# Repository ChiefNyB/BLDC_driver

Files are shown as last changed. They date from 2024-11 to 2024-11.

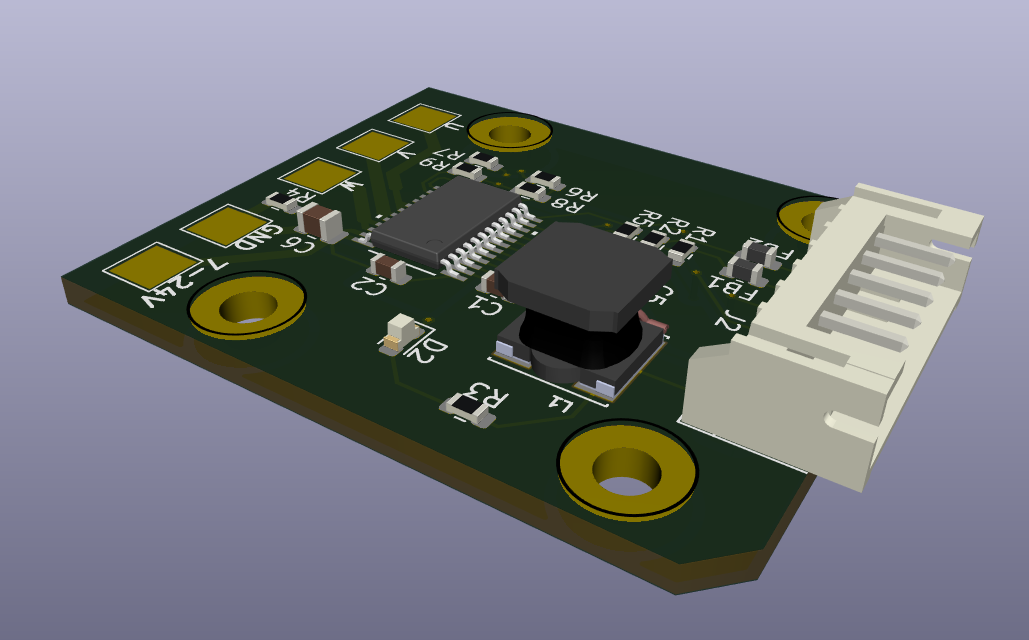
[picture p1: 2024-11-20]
assets/assembly2.png

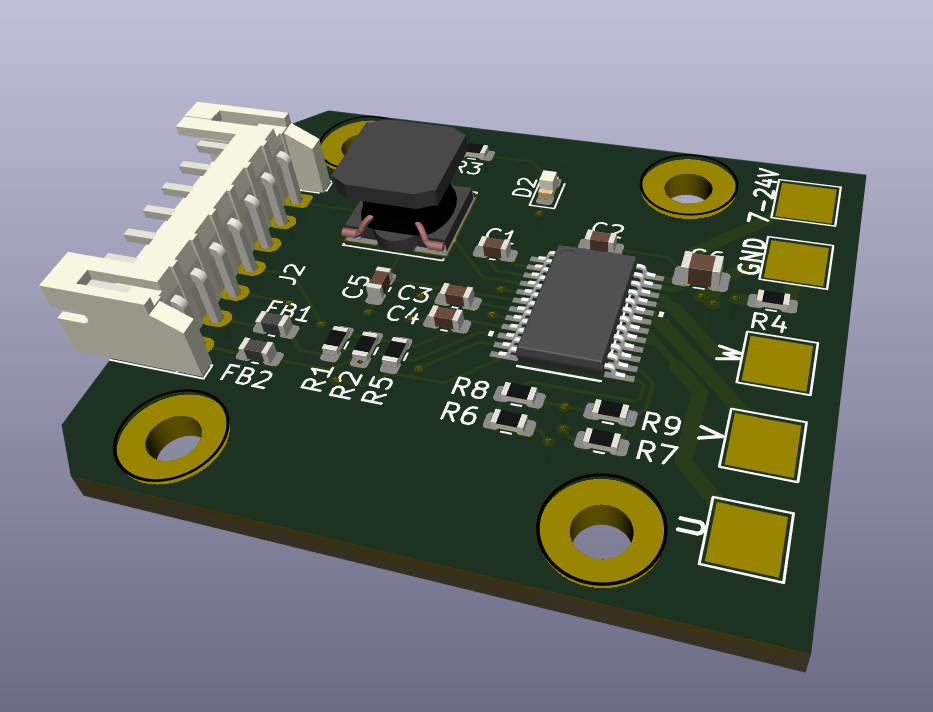
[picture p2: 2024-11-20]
assets/assembly.png

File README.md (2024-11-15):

# BLDC driver
 [TI DRV10983-Q1](https://www.ti.com/product/DRV10983-Q1/) based BLDC motor controller

 Development software: KiCad 8.0.5 (latest)

 ## *Üzenet*

 Szerintem majd ide a README-be írogathatjuk dokumnetáció vázlatos részét,
 a számítást meg Excelbe vagy valami python scriptbe lehet nyomni
 (ugyanígy version controllozva), aztán innen aztán mehet majd Word-be a bővebb leírás.

 Éés szerintem nyugodtan írogathatunk ide kommenteket is, talán kevésbé veszik
 el mint a chatben.

 Légyszi nézzétek meg a katalógust is (bent van a datasheet mappában), meg az áramkört is,
 igyekeztem leírni a dolgokat amiket csináltam. Mindezek alapján remélem, hogy nektek is érthető lesz majd, hogy mi mit csinál.
 Ha bármi kérdésetek van, írjátok akár ide valahova, akár messengeren. Légyszi mindketten olvassátok el az egész README-t!
 Köszi :)

 Ide kigyűjtöttem, hogy szerintem még mi kell:

 ## További lépések (nagy vonalakban)

  - Komponensek értékeinek kiszámítása --> komponensek választása
  - Fizikai layout kialakítása
  - (adhatnánk majd a hozzá passzoló motorokra egy példát)

## Dokumentáció vázlatosan (kapcsolás)
(ömlesztett gondolatok, egy csöppet össze-vissza)

KORREKCIÓ: A TVS DIÓDÁT EGYENLŐRE KISZEDTEM, VAN BEÉPÍTETT A CHIPBE
  
  - a chip modellt (footprint, stb...) a
  TI-os lapról töltöttem és illesztettem be: [link](https://vendor.ultralibrarian.com/TI/embedded/?gpn=DRV10983-Q1&package=PWP&pin=24&sid=&c=0)
  (lementettem saját global libraryba... ha nektek valami miatt nem látszódna, akkor
  ezt lehet nektek is meg kell csinálni)
  - IC bekötése a datasheet 64. oldalán található 71.figureban, egy csomó komponens (főleg kondik) értéke innen van
  található kapcsolás alapján (lehet arról írni esetleg, hogy milyen funkciói vannak
  az IC-nek)
    - 12Vról megy, (esetleg 24V, de ha 28-ig visszatölt, akkor már egyébként lekapcsolja a powerstaget)
    - I2C max 400kHz
    - milyen lekapcsolási-biztonsági funkciók vannak (Over voltage, o.current, thermal shutdown...)
  - a schematic hierarhikus, több lapból áll (drive, power), de nem is biztos hogy szükség lenne rá, mert elég egyszerű,
  csak kicsit fancybb és esetleg segíti a logikát átlátni
  - a pontos típus: [DRV10983SQ](https://www.ti.com/product/DRV10983-Q1/part-details/DRV10983SQPWPRQ1) legyen, ha standby modeban is 
  használni szeretnénk az 5V-os buck convertert --> mikrovezérlő meghajtható róla (ld. katalógus 3.o.)
  - I2C védelmet és szűrést [ez](https://www.we-online.com/components/media/o734709v410%20ANP121a%20%20Filter%20and%20surge%20protection%20for%20I2C%20Bus%20EN.pdf)
  alapján csináltam --> itt javasolt komponensekkel (ferrit gyöngy és TVS dióda) megegyező paraméterűeket lesz majd érdemes választani
  (egyenlőre egy kb hasonlót raktam be)
  - terveim szerint csinálok 2 verziót:
    - csatlakozós (Táp & motor is csatlakozós)
    - beforrasztós (táp& motornak csak pad-ek vannak amikre majd rá lehet forrasztani a vezetékeket)
    (ez az ahol a testpoint (TP) nevű kivezetések vannak)
  - a TI IC alatt a túloldalon van egy PAD (majd thermal viákkal összekötve) a GND-hez kötve, hogy hőt disszipáljon
  és ide lehet(ne) rakni majd a hűtőbordát is
  - van egy sima GND és egy PWRGND, hogy a motor áramai minél kevésbé zavarjanak bele a digitális jelekbe, ezek össze vannak kötve egy 0ohmos ellenállással
  - az 5V (output) jelenlétét LED jelzi
  - decoupling capacitorok közel az IC-hez (majd a kialakításnál fizikailag)
  - minden jel-bemenet és kimenet, ami ki van vezetve (SCL, SDA, FG, SPEED, DIR) 3V3 TVS diódával védve ESD ellen
  - I2C csak 3V3 szinten mehet
  - FG pin 3V3-as impulzusokat ad (to be checked in datasheet)
  - DIR és SPEED bemeneten használható 5V-os jel (azaz megtáplálható egy sima potiról és kapcsolóról, ennek az egy panelnek a segítségével)
    - viszont ehhez előbb I2C-n be kell konfigurálni
    - a bemenetek egy-egy feszültségosztóval le vannak skálázva 3v3-ra
    - ehhez majd lesznek számítások, poti értéke
  - a legvégén esetleg kérhetünk majd árajánlatot ha unatkozunk :P

  - az I2C-t úgy lehet használni, ha a külső áramkör GND-je össze van kötve a motordriver GND_D-jével
  - az 5V-os bemenet használatához is legalább a GND-t kell bekötni

  ## Szükséges számítások, paraméterek
  Légyszi Kristóf ide, vagy valami fileba majd gyűjtsd ki a komponens nevét/számát (pl.: R1) és a linket hogy melyiket választottuk...
  Majd belepakkolom a schematicba és generálok belőle egy BOM .csv filet.
  ( Lehetséges oldalak: farnell, rs-online, lomex, TME ...ilyesmik. Csak legyen magyar oldal! )
  (Esetleg lehet egy specifikus motor amit kinézünk, és annak a pramaétereit is felhasználjuk a számításokhoz)

  - elsősorban a TI-os katalógus alapján, a typical application résznél van egy lista hogy ők mit javasolnak
  - csak SMD alkatrészeket please
  - alapból ilyen 0603-as (mármint inches 0603, mert a metrikus méretek el vannak tolva) méretű ellenállásokat és kondikat stb. keresünk,
  esetleg kicsit kisebb vagy nagyobb (de nyilván ha nagyobb kell, akkor nagyobb kell, pl valszeg a táp kondija az gyanús, hogy nagyobb)
    - ellenállás választásnál ki kell számolni a teljesítményét és aszerint kell választani (0.25W; 1W ...)
    - LED-nél választani kell egy LED-et, majd az ahhoz előírt mA-hez választunk egy ellenállást, a színét rád bízom Kristóf ;)
    - kondiknál a feszültséget és a kapacitást kell nézni alapból
    - SPEED és DIR inputokra olyan feszültségosztó kell (ellenállásértékek), amik leskálázzák a bejövő 5V-ot 3,3-ra
  - I2C védelem: ld. dokumentáció vázlatpontjai közt, illetve ezek alapján még újra számíthatók a felhúzó ellenállások értékei is
  - ha nagyon fancy-k akarunk lenni, egy thermal calculationt is nyomhatunk és esetleg egy hűtőbordát is válasszunk (1. gyakorlat -> pdf kb. 10. oldal)
  - TVS diódák kapcsolása nem látszik a kapcs rajzon de az assets mappában megtalálható

  ## Kiválasztott alkatrészek
  Feltöltöttem egy Excel táblában a katalógusokból kiválasztott áramköri elemeket. A dokumentációhoz ideírom, amit csináltam:

  - Katalógusból kiválasztottam az ajánlások miatt előre ismert áramköri elemeket + a LED-et
  - Három kis számolás volt:
    - LED ellenállás,
    - feszültségosztók (TI online számolójával: [link](https://www.ti.com/download/kbase/volt/volt_div3.htm)),
    - I2C felhúzó ellenállások min-max értékeinek újraszámolása (az ajánlottak jók maradtak).

  Minden számolás és az összes alkatrész az Excelben. Alkatrészekhez van típuszsám, link, footprint adat és méretezési feltétel is (ha volt).
  A termikus számítások nem voltak kivitelezhetők, nincs elég adat veszteségekre vagy case-sink hőellenállásra (vagy hogy egyáltalán becsüljük).
  Elvileg a driver alá kerülő thermal pad elegendő, bele lehet írni a dokumentációba, hogy igény szerint lehet még adni hozzá.

  ## PCB alias NYÁK design
  - csatolásmentesítő kondik közel az IC-hez, mindegyiknek saját viája van a GND-hez
  - 45°-os track törésszögek a jelreflexió elkerülésére
  - thermal via-k: 20mil hole diameter, 8mil hole (for least resistance) ahogy [itt](https://www.ti.com/lit/an/slva959b/slva959b.pdf) a 2.5-ben írják
  - a teljesítményfolyamban lévő track-ek és viák méretezve vannak (viából van egy dupla is, bár nem feltétlen lenne rá szükség) 
  a számításokról készített screenshot az assetsben
  - digitális <--> teljesítény oldalak elválasztása fizikailag amennyire lehet
  - teljesítményvonalak kialakításánál fontos volt, hogy minél kisebb loopot csináljanak és rövidek legyenek
  - GND és GNDPWR egy 0ohmos ellenállással (R4) összekötve: kis vezetékellenállású összeköttetés a bemeneti GND és a digitális jelek
  GND-je közt
  - buck konverter trackjei default értéken vannak, de van róla számítás hogy elég (assetsben)
  - a power bemenetek jelölve vannak, a csatlakozónál légyszi csinálj egy ábrát, ami "katalógusba" mehetne
  - két sarokban letörések...mert csak... :P 
  - M2.5-ös mounting holeok hogy lehessen odacsavarozni valahova
  - az alsó oldalra ragasztható heatsink ha akarja a felhasználó, de figyelni kell,
  hogy ezen a részen galvanikus kapcsolat ne alakuljon ki a külvilággal
  - földkiöntés a sima GND-vel
  (- esetleg át lehetne alakítani hogy a heatsink-pad a sima GND-hez kapcsolódjon és a PWRGND-t másmerre vezetni, ha van idő...)
  - ... és ezeken kívül bármi amit látsz a boardon és érdemes leírni

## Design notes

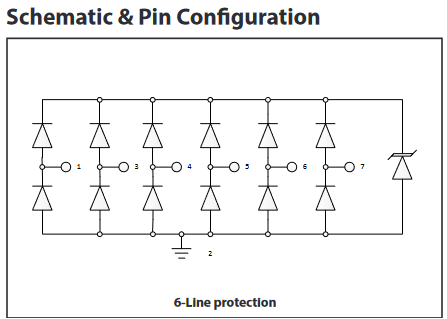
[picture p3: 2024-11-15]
assets/TVS_schematic.png

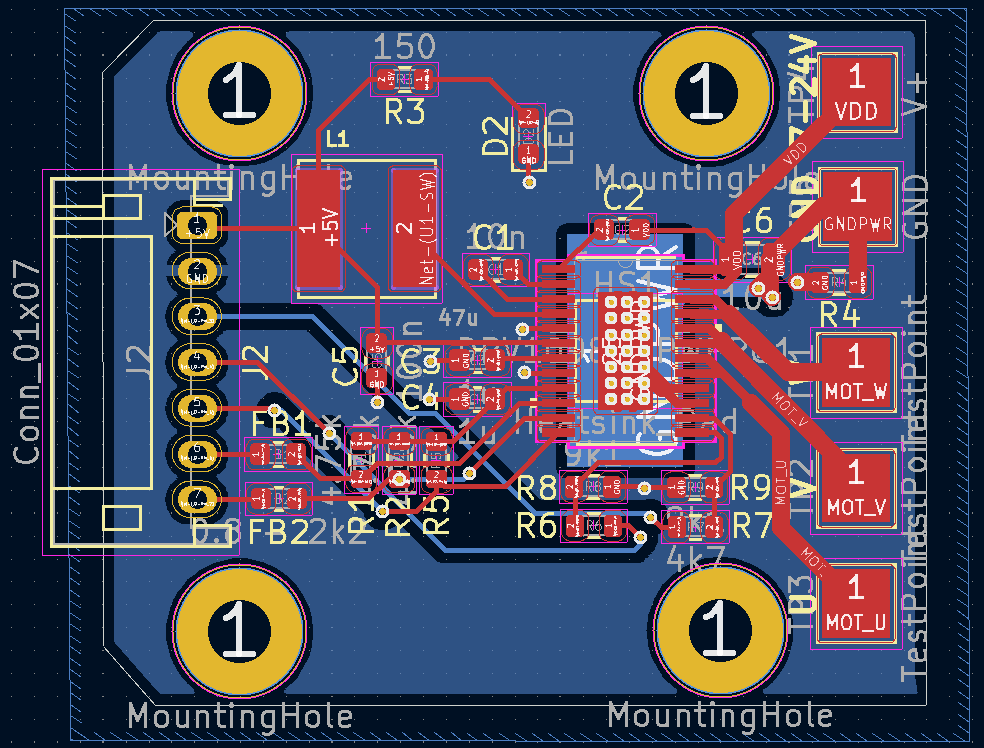
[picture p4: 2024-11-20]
assets/PCB_design.png

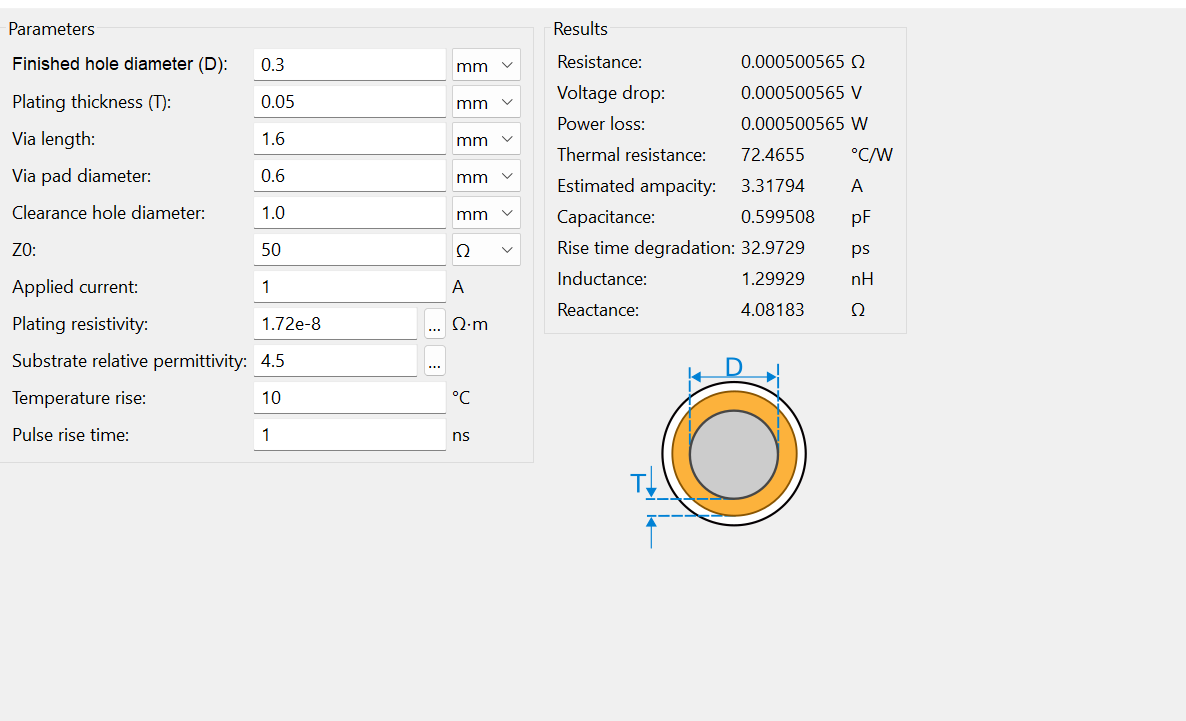
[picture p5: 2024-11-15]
assets/via current calculation.png

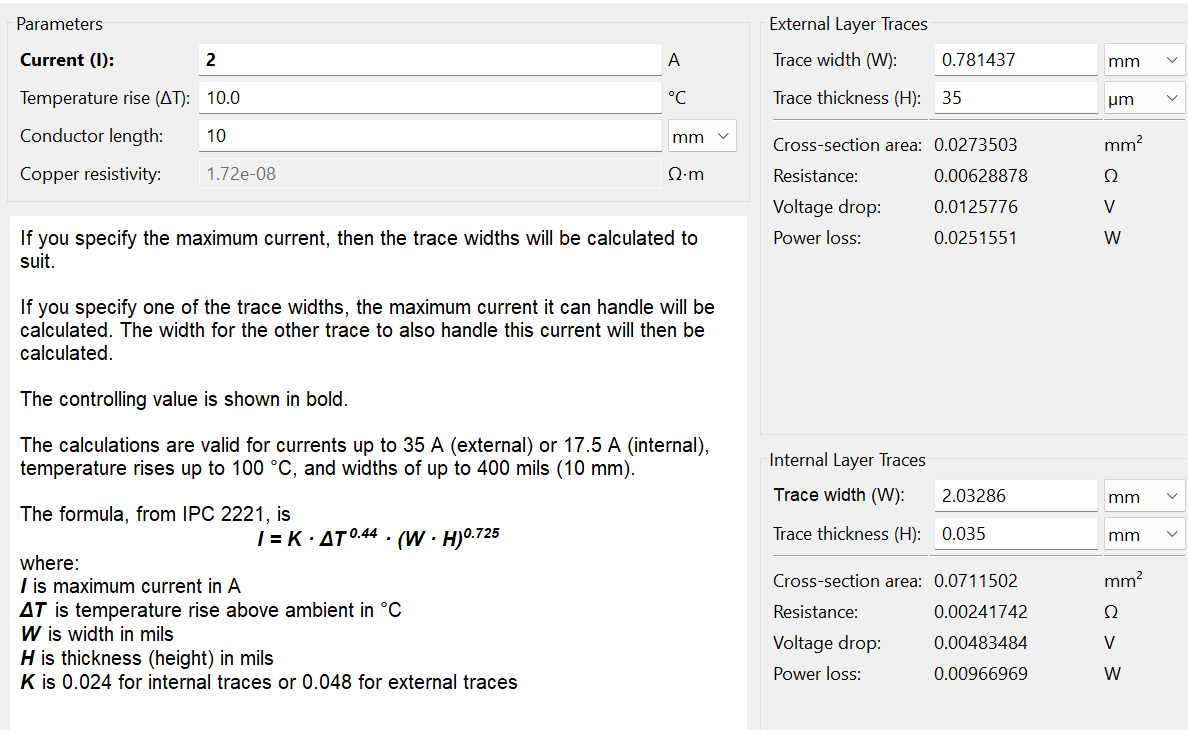
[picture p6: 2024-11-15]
assets/track width calculation.png

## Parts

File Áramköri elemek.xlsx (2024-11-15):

Jelölés | Érték | Típus | Link | Footprint |  | Méretezve
C1 | 10n | CC0603KPX7R0BB103 | https://hu.farnell.com/yageo/cc0603kpx7r0bb103/capacitor-0-01uf-x7r-0603/dp/4255277 | Van letölthető | 0603 | Max VCC = 48 V, biztosági tényezővel < 100 V
C2 és C5 | 100n | GRM188R72A104KA35D | https://hu.farnell.com/murata/grm188r72a104ka35d/cap-0-1-f-100v-10-x7r-0603/dp/1828921 | Van letölthető | 0603 | Max VCC+6 V < 100V
C3 és C4 | 1u | CC0603KRX7R7BB105 | https://hu.farnell.com/yageo/cc0603krx7r7bb105/cap-1-f-16v-10-x7r-0603/dp/1458900 | Van letölthető | 0603 | Max V3P3, biztonsági tényezővel < 16 V
C6 | 10u | GRM188R61E106KA73D | https://www.digikey.hu/hu/products/detail/murata-electronics/GRM188R61E106KA73D/9867922 | Van letölthető | 0603
L1 | 47u | VLS6045EX-470M | https://www.digikey.hu/hu/products/detail/tdk-corporation/VLS6045EX-470M/5286703 | Van letölthető | 0645 | Min. 1.15A, max. 1 Ohm |  | U_max
R1, R2 és R5 | 4.75k | RC0603FR-074K75L | https://hu.farnell.com/yageo/rc0603fr-074k75l/res-4k75-1-0-1w-0603-thick-film/dp/3495864 | Van letölthető | 0603 | 0.003368421053 | W | 4 | V
R3 (LED) | 150 | RC0603FR-07150RL | https://hu.farnell.com/yageo/rc0603fr-07150rl/res-150r-1-0-1w-0603-thick-film/dp/9238387 | Van letölthető | 0603 | 0.06 | W | 0.02 | A
R4 | 0 | RC0603FR-130RL | https://hu.farnell.com/yageo/rc0603fr-130rl/res-1a-0-1w-thick-film-0603/dp/4312015RL | Van letölthető | 0603
R6 és R7 | 4.7k | AT0603BRB074K7L | https://hu.farnell.com/yageo/at0603brb074k7l/res-4k7-0-1-0-1w-thin-film-0603/dp/4047053 |  | 0603 | 0.005319148936 | W | 5 | V
R8 és R9 | 9.1k | AT0603BRD079K1L | https://hu.farnell.com/yageo/at0603brd079k1l/res-9k1-0-1-0-1w-thin-film-0603/dp/4047064 |  | 0603 | 0.001196703297 | W | 3.3 | V
D1 | TVS diode array | PESD4USB3UTTS-QX | https://hu.mouser.com/ProductDetail/Nexperia/PESD4USB3UTTS-QX?qs=3Rah4i%252BhyCFcdVR8DwXcmg%3D%3D | Van letölthető | DFN-2510D-10 | 3.3 V operating voltage
D2 | LED | 150060VS55040 | https://www.digikey.hu/hu/products/detail/w%C3%BCrth-elektronik/150060VS55040/8557182 | Van letölthető | 0603
FB1 és FB2 | – | 782631222 | https://hu.farnell.com/wurth-elektronik/782631222/ferrite-bead-2-2-kohm-0-15a-0603/dp/3551396 | Van letölthető | 0603
Számolás
R3
Continuous Forward Current | 0.02 | A
Niytóirányú feszültség | 2.0 | V
Forrásfeszültség | 5.0 | V
LED ellenállás: | 150 | Ohm
Feszültségosztók
U_be | 5 | V
U_ki | 3.3 | V
Kalkulátor: | https://www.ti.com/download/kbase/volt/volt_div3.htm
 | (Standard méretű ellenállások kereséséhez feszültségosztóhoz)
R1 | 4.7k | Ohm
R2 | 9.1k | Ohm
I2C felhúzó ellenállások (f = 400 kHz)
Referencia-feszültség | 3.3 | V (dokumentációból)
Maximum logikai 0 feszültség | 0.6 | V (dokumentációból)
Max parazita busz-kapacitás | 6.5e-13 | F (400 kH)
Maximum engedélyezett felszállási idő | 3e-07 | s (400 kHz)
Maximum lehetséges áram | 0.003 | A (400 kHz)
R_min | 900 | Ohm
R_max | 544716.7019 | Ohm
Maradhat a 4.75 kOhm

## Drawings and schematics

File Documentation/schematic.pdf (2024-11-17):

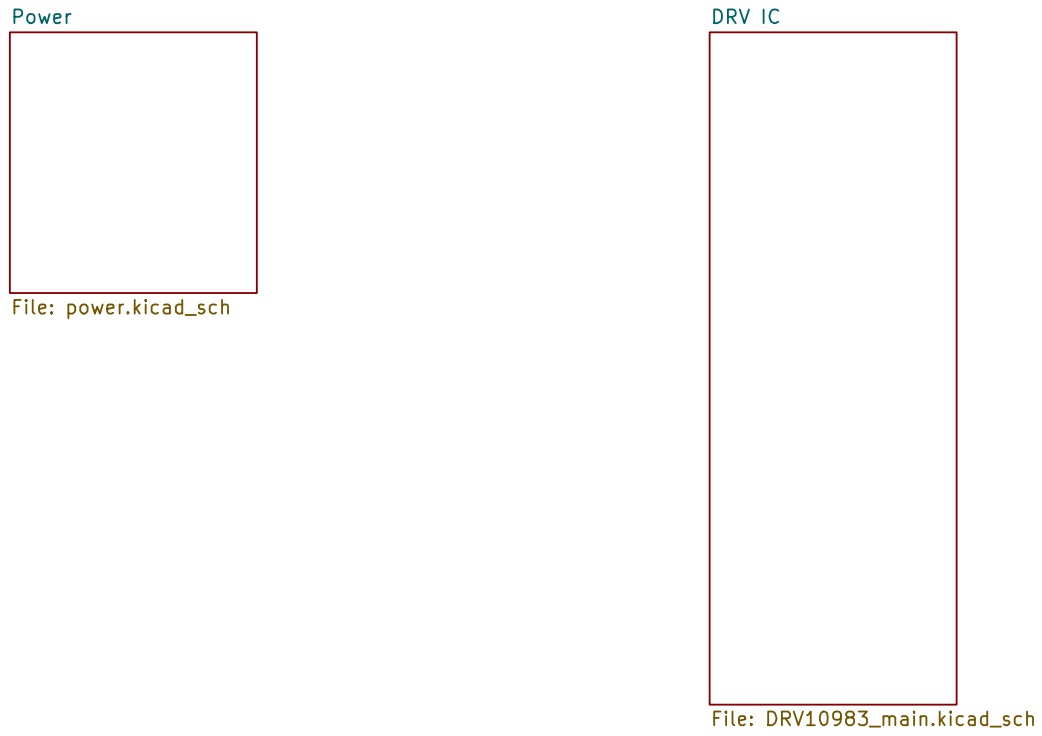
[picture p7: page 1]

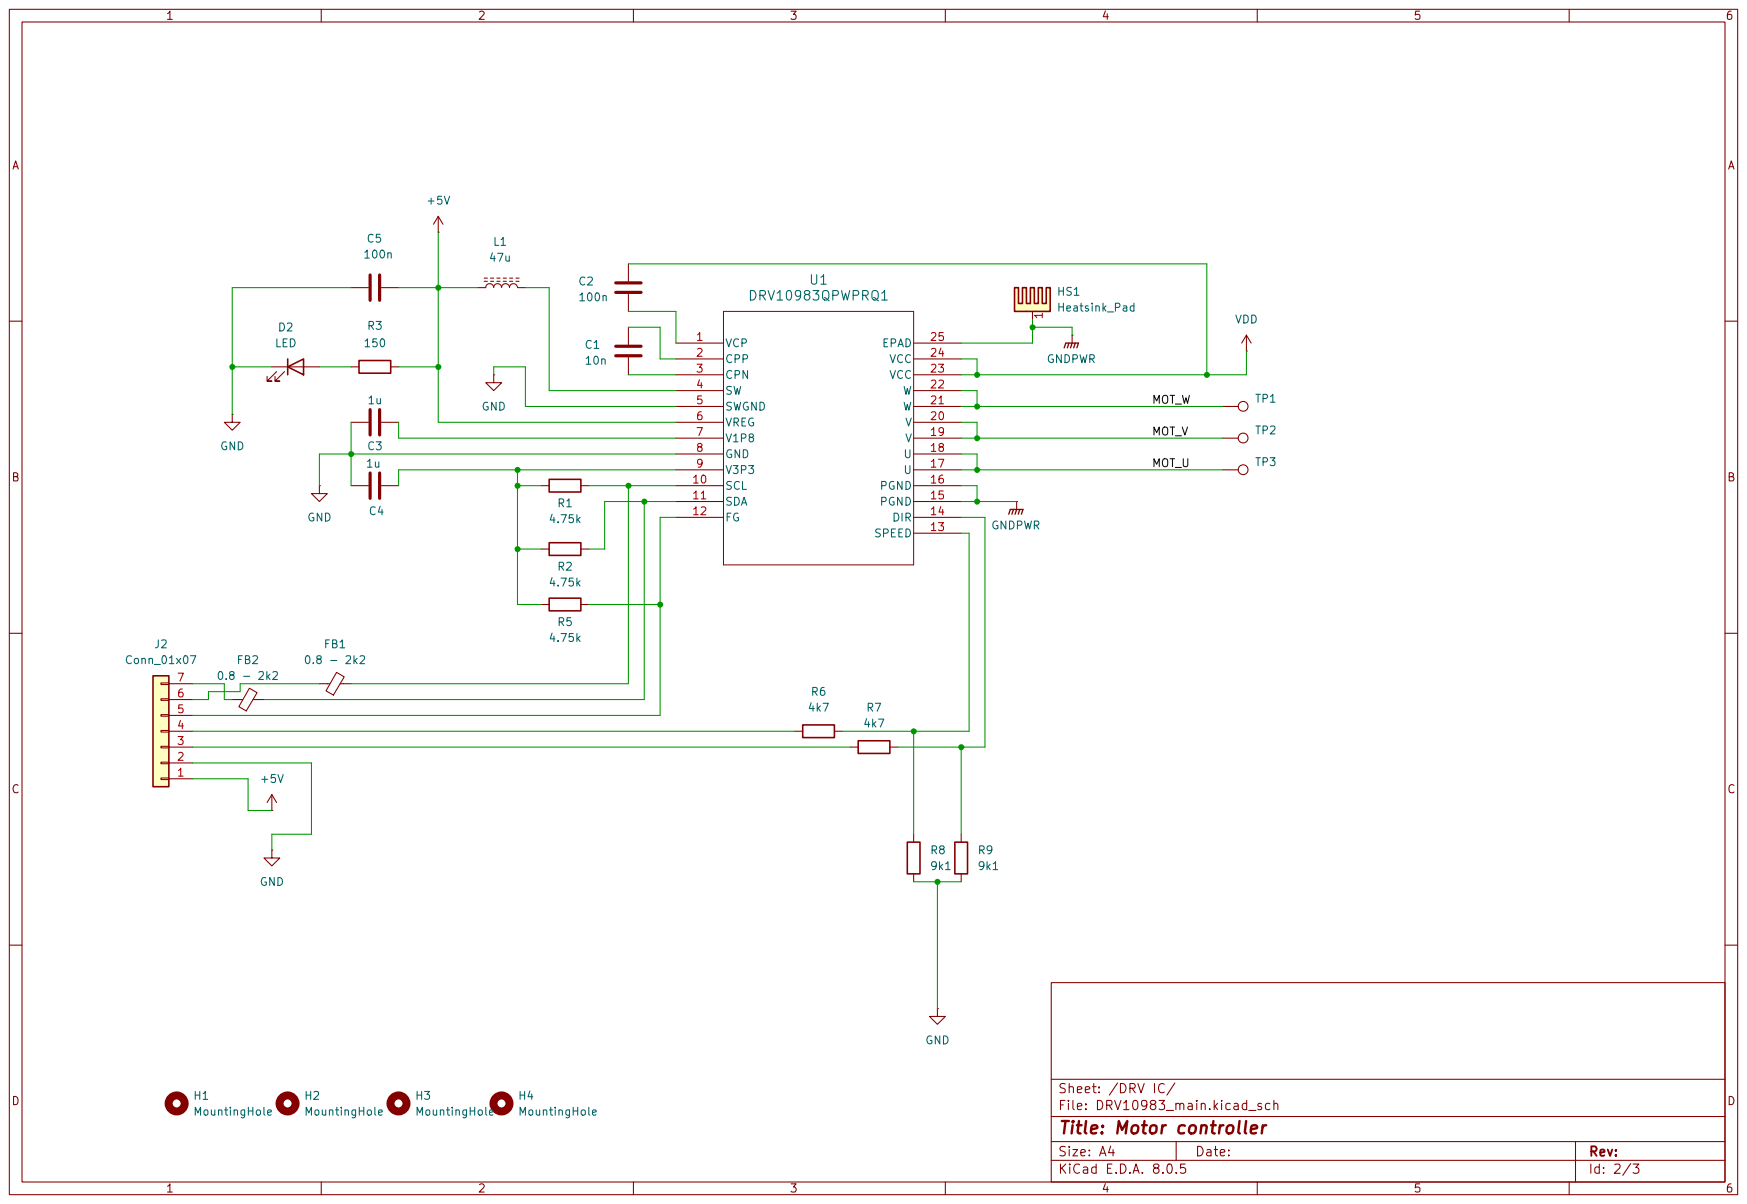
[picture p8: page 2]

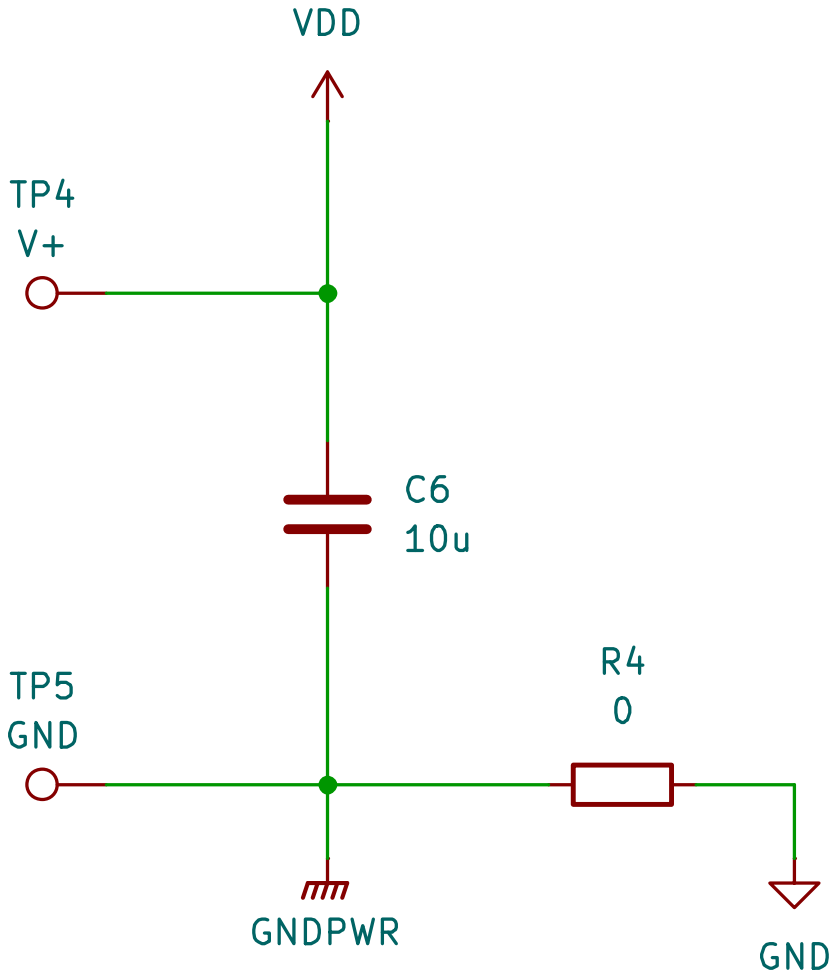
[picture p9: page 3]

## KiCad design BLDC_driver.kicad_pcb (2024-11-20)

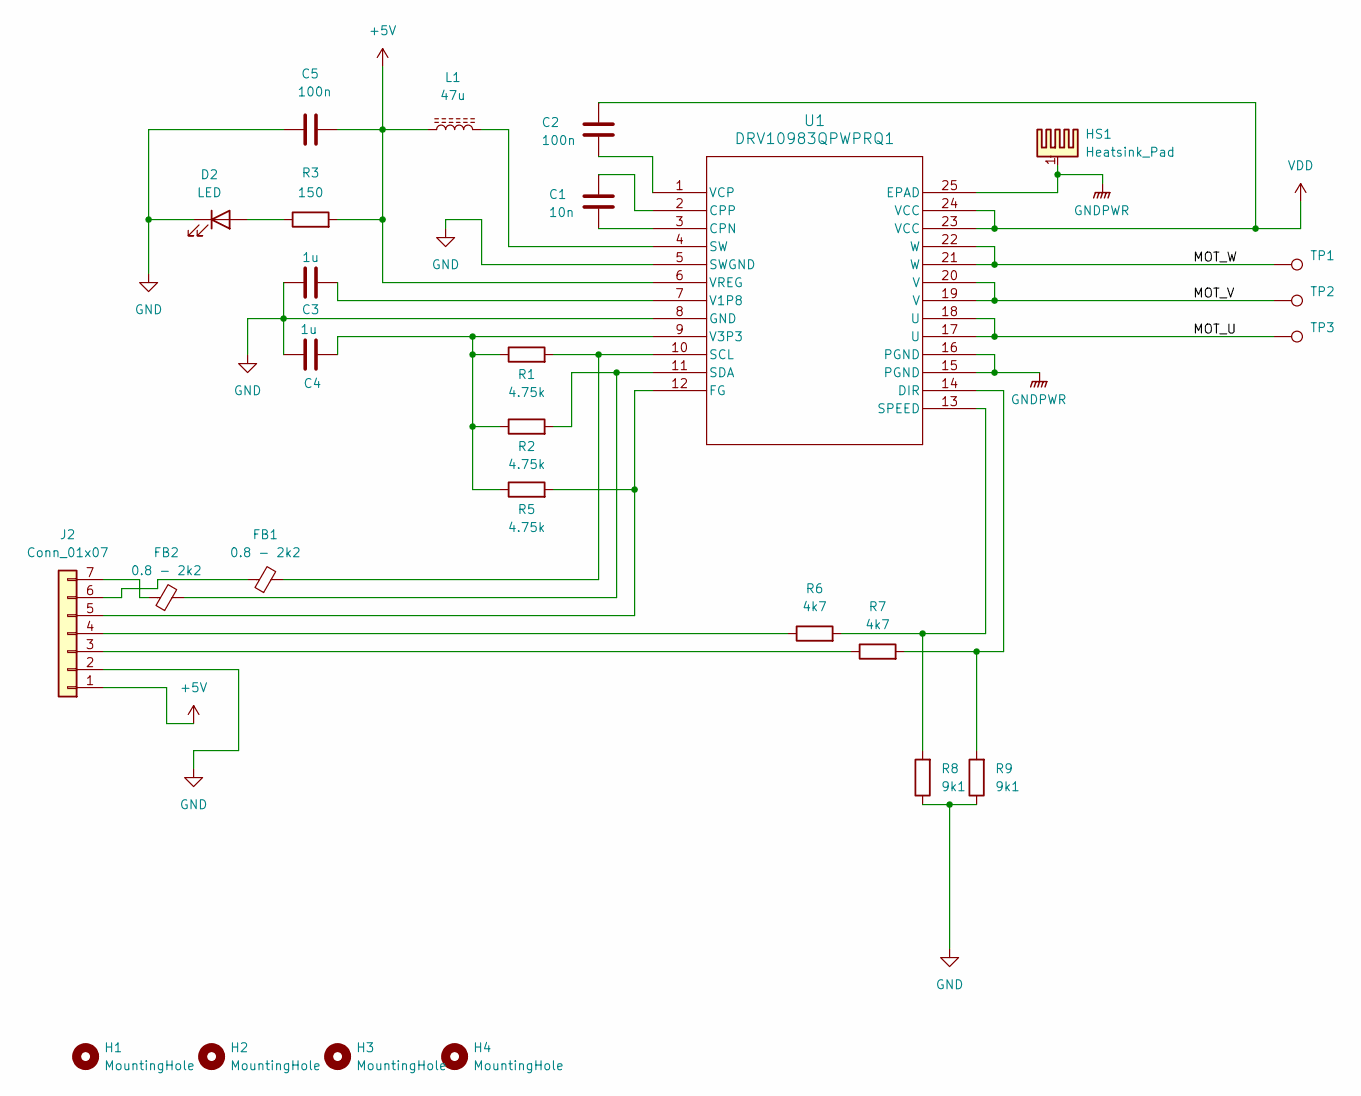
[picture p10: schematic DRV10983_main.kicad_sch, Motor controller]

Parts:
C1: 10n; C_0603_1608Metric
C2, C5: 100n; C_0603_1608Metric
C3, C4: 1u; C_0603_1608Metric
D2: LED; LED_0603_1608Metric
FB1, FB2: 0.8 - 2k2; L_0603_1608Metric
H1, H2, H3, H4: MountingHole; MountingHole_2.7mm_Pad
HS1: Heatsink_Pad; TestPoint_Pad_4.0x4.0mm
J2: Conn_01x07; JST_PH_S7B-PH-K_1x07_P2.00mm_Horizontal
L1: 47u; IND_VLS6045EX-470M
R1, R2, R5: 4.75k; R_0603_1608Metric
R3: 150; R_0603_1608Metric
R6, R7: 4k7; R_0603_1608Metric
R8, R9: 9k1; R_0603_1608Metric
TP1, TP2, TP3: TestPoint; TestPoint_Pad_3.0x3.0mm
U1: DRV10983QPWPRQ1; PWP24_2P4X5P16_TEX

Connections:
+5V: C5.2, J2.1, L1.1, R3.2, U1.6 (VREG)
/DRV IC/MOT_U: TP3.1, U1.17 (U), U1.18 (U)
/DRV IC/MOT_V: TP2.1, U1.19 (V), U1.20 (V)
/DRV IC/MOT_W: TP1.1, U1.21 (W), U1.22 (W)
GND: C3.1, C4.1, C5.1, D2.1 (K), J2.2, R8.1, R9.1, U1.5 (SWGND), U1.8 (GND); also elsewhere on the board
GNDPWR: HS1.1, U1.15 (PGND), U1.16 (PGND), U1.25 (EPAD); also elsewhere on the board
unnamed: D2.2 (A), R3.1
unnamed: J2.3, R7.1
unnamed: J2.4, R6.1
unnamed: J2.5, R5.2, U1.12 (FG)
unnamed: FB1.1, J2.6
unnamed: FB2.1, J2.7
unnamed: C1.2, U1.3 (CPN)
unnamed: C1.1, U1.2 (CPP)
unnamed: R7.2, R9.2, U1.14 (DIR)
unnamed: FB1.2, R1.2, U1.10 (SCL)
unnamed: FB2.2, R2.2, U1.11 (SDA)
unnamed: R6.2, R8.2, U1.13 (SPEED)
unnamed: L1.2, U1.4 (SW)
unnamed: C3.2, U1.7 (V1P8)
unnamed: C4.2, R1.1, R2.1, R5.1, U1.9 (V3P3)
unnamed: C2.2, U1.1 (VCP)
VDD: C2.1, U1.23 (VCC), U1.24 (VCC); also elsewhere on the board

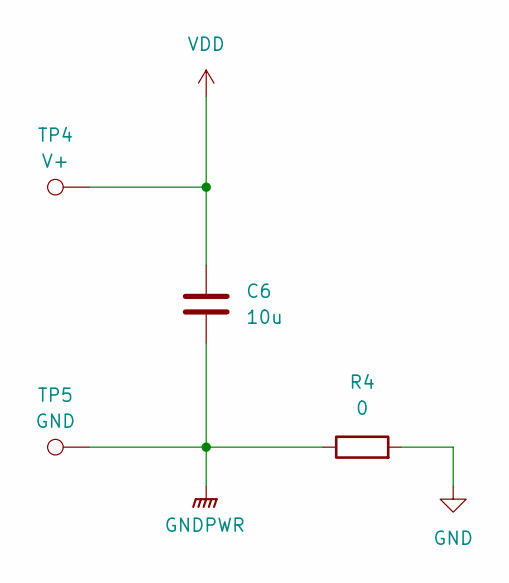
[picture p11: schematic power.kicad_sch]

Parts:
C6: 10u; C_0805_2012Metric
R4: 0; R_0603_1608Metric
TP4: V+; TestPoint_Pad_3.0x3.0mm
TP5: GND; TestPoint_Pad_3.0x3.0mm

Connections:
GND: R4.2; also elsewhere on the board
GNDPWR: C6.2, R4.1, TP5.1; also elsewhere on the board
VDD: C6.1, TP4.1; also elsewhere on the board

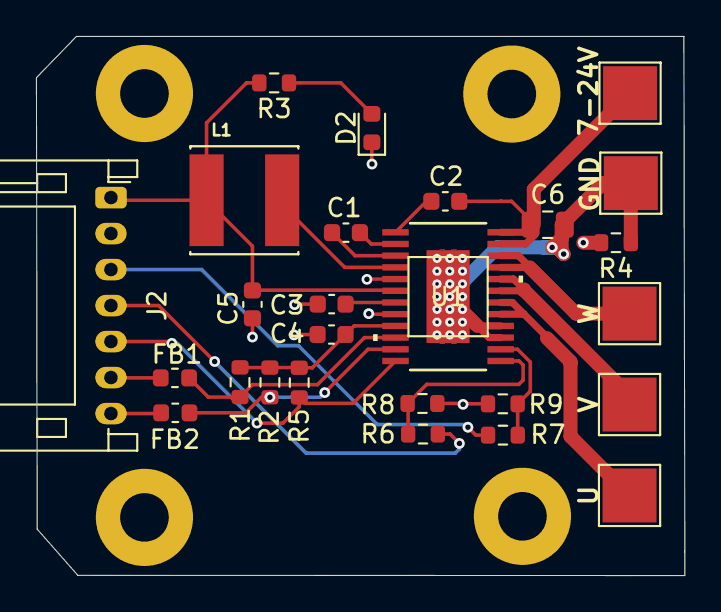
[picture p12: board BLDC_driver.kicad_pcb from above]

Board: 2 copper layers, 36.0 x 29.9 mm, 31 parts (0 on the bottom side), 23 nets.

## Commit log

2024-10-11 Empty project added
    [BLDC_driver.kicad_pcb, BLDC_driver.kicad_sch]
2024-10-14 Driver schematic ready
    [BLDC_driver.kicad_sch, DRV10983_main.kicad_sch, power.kicad_sch]
2024-10-19 Schematic complete
    Completed power and controller sub-schematics, ESD protection
    Not completed: componenet values and footprints
    Not started: PCB layout design
    [BLDC_driver.kicad_sch, DRV10983_main.kicad_sch, power.kicad_sch]
2024-11-15 PCB v1 complete
    with images, README extended...
    [BLDC_driver.kicad_pcb, DRV10983_main.kicad_sch, power.kicad_sch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]
2024-11-20 C6 capacitor reviewed
    [BLDC_driver.kicad_pcb, power.kicad_sch]
